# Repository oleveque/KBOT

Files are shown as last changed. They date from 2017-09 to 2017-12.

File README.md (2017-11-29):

# KBOT

Un KBOT est un petit "robot sandwich" doté de deux roues motrices (moteurs+codeurs), d'une Arduino Méga 2560, d'un écran LCD 16x2, d'une batterie 3S… C'est une fabrication maison que réalise les premières années du club de robotique de l'ENS Paris-Saclay pour acquérir les bases de la robotique & se familiariser avec la programmation à travers l'IDE Arduino.
Pour plus d'information consultez notre site [[Kro]bot](https://wiki.crans.org/ClubKrobot).

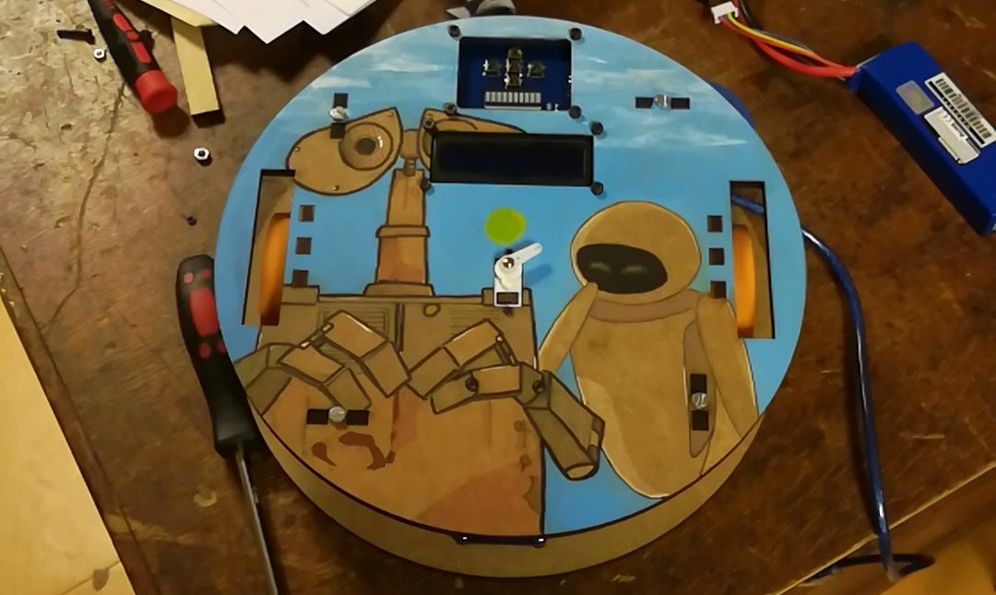
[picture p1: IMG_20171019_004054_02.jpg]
KBOT_V2


## Informations générales :
* *Mode de déplacement du robot :* entraînement différenciel
* *Moyens de communication :* USB, Bluetooth
* *Version actuelle :* 2.0 (Révisé par Y. Labbe & O. Lévêque - Sept. 2017)

## Ports I/O :
* 1 module Bluetooth (HC-06) ;
* 1 port SHARP (GP2D12) ;
* 1 port Servo (SG90) ;
* 1 port pour controler le niveau de charge de la batterie ;
* 1 Buzzer ;
* 1 port extension pour 5 Boutons ;
* 1 port extension pour 10 Leds.

## Amélioration pour la version 2.1 :
* CAO -> simplifier les entretoises des roues + ajuster l'empreinte de l'écran LCD + ajouter un système de fixations pour les cales avant/arrière
* PCB -> corriger l'agencement buzzer/bluetooth + corriger les couleurs des fils des encoders + changer le sens de la nappe PowerDistributor-PropulsionShield + changer le sens de connecteur batterie + amener la led 13 sur le UI
* Arduino -> Ajouter 1 exemple d'Asserv

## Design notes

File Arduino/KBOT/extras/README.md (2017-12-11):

# KBOT + BRAINZY

Vous pouvez utiliser la bibliothèque BRAINZY pour programmer votre KBOT : http://github.com/oleveque/BRAINZY
Une documentation complète de cette bibliothèque est disponible : http://docs.mr-robotics.com

## Installation

Une fois la bibiliothèque BRAINZY installée sur votre ordinateur, il ne reste plus qu'à remplacer les fichiers
`BRAINZY > src > utility > configRobot.h` et `BRAINZY > src > utility > config_v3.0.h` par les deux fichiers fournis dans `KBOT > extras`.
N'oubliez pas de faire correspondre les fichiers changés avec ceux appelés par le fichier `BRAINZY > src > BRAINZY.h`.

Enjoy & have a lot of fun...
Made with love by [Kro]bot team.

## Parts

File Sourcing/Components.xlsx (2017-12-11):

 | Batch ($) | Qty (Batch) | Unit ($) | Unit (€) | Qty | TOT 1 KBot (€) | Mots clés (Recherche ebay/Aliexpress)
Composants mécaniques & éléctrique
Moteur (http://www.robotshop.com/eu/fr/moteur-12v-150rpm-a-engrenage-301-avec-encodeur.html) |  |  |  | 21.86 | 2 | 43.72
Hex mount (http://www.robotshop.com/eu/fr/moyeu-hex-6mm-1l.html) |  |  |  | 4.31 | 2 | 8.62
Roue 2-7/8" (http://www.robotshop.com/eu/fr/rb-ban-94-roue-orange.html) |  |  |  | 3.2 | 2 | 6.4
Arduino Mega 2560 (https://fr.aliexpress.com/item/Free-Shipping-MEGA2560-R3-MEGA2560-REV3-ATMEGA2560-16AU-Board-USB-Cable-compatible-We-are-the-manufacturer/32513419382.html) |  |  | 9.57 | 8.12 | 1 | 8.12 | Arduino Mega 2560
Pont (dual) L298N (https://www.aliexpress.com/item/Free-Shipping-10pcs-lot-L298N-Dual-Bridge-DC-stepper-Controller-Control-Motor-Driver-module-Board/32581277003.html) | 14.85 | 10 | 1.49 | 1.26 | 1 | 1.26 | L298N
Chargeur (http://www.ebay.com/itm/iMaxRC-iMax-B3-Pro-Compact-2S-3S-Lipo-Balance-Battery-Charger-For-RC-Helicopter-/172802158295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) |  |  |  | 4 | 1 | 4 | Lipo 3S charger
Batterie 3S-2200 mAh (https://hobbyking.com/fr_fr/turnigy-2200mah-3s-25c-lipo-pack.html) |  |  |  | 9.36 | 1 | 9.36
1602 LCD + I2C (https://www.aliexpress.com/item/1602-16x2-HD44780-Character-LCD-w-IIC-I2C-Serial-Interface-Adapter-Module/32709905064.html) |  |  |  | 1.46 | 1 | 1.46 | 1602 lcd + i2c
Bluetooth (https://www.aliexpress.com/item/4pin-hc-06-Bluetooth-transmission-module-including-base-plate-belt-enable-and-output-radio-serial/32265012433.html) |  |  |  | 1.46 | 1 | 2.4 | HC-06
Servomoteur 9G SG90 (https://fr.aliexpress.com/item/Free-Shipping-10pcs-lot-Special-promotions-SG90-9g-Mini-Micro-Servo-for-RC-for-RC-250/32320058558.html) |  |  | 1.22 | 1.04 | 1 | 1.04 | SG90 9G
Sharp 10-80cm (https://fr.aliexpress.com/item/IR-Sensor-GP2Y0A21YK0F-Measuring-Detecting-Distance-Sensor-10-to-80cm-with-Cable-for-Arduino/32462134213.html) |  |  |  | 3.1 | 1 | 3.1 | Sharp sensor 10-80cm
Sous-total |  |  |  |  |  | 89.48
Connectique
Nappe JST 2.54mm f-f 4pin 20cm Power <-> Shield (https://www.aliexpress.com/item/100-SETS-JST-XH-2-54mm-2-3-4-5-6-7-8-9-10-Pin/32794829177.html) | 20.89 | 100 | 0.21 | 0.18 | 1 | 0.18 | Jst wire double end
JST 2.54mm 4 pin connecteur m (https://fr.aliexpress.com/item/150Pcs-2-54Mm-Pitch-Male-4-Pins-Rc-Lipo-Battery-Balance-Connector-Jst-Xh-Header/32768115241.html) | 2.91 | 150 | 0.02 | 0.02 | 2 | 0.03
Nappe JST2.0 mm f-f 3pin 20cm Sharp <-> Shield (https://www.aliexpress.com/item/100-SETS-JST-PH-2-0mm-2-3-4-5-6-7-8-9-10-Pin/32797675782.html) | 19.94 | 100 | 0.2 | 0.17 | 1 | 0.17 | Jst wire double end
JST 2.0mm 3 pin connecteur m (http://www.ebay.com/itm/JST-PH-2-0mm-3-Pin-Male-and-Female-Housing-Connector-with-Crimps-x-50-Sets-/122329707743) | 6.17 | 50 | 0.12 | 0.1 | 1 | 0.1
Nappe Dupont f-f 4pin 20cm I2C-Screen <-> Shield (https://www.aliexpress.com/item/NEW-10pcs-lot-Keyestudio-4-PIN-20CM-jumper-wire-dupont-cable-for-arduino-breadboard-free-shipping/32706947085.html) | 2.66 | 10 | 0.27 | 0.23 | 1 | 0.23 | Dupont 4 pin wire
Fil dupont vert f-f 20cm Moteur G <-> Shield (https://www.aliexpress.com/item/Free-shipping-100pcs-New-1p-to-1p-20cm-Green-female-to-female-jumper-wire-Dupont-cable/1790303724.html) | 5 | 100 | 0.05 | 0.04 | 2 | 0.08 | female to female dupont green wire
Fil dupont bleu f-f 20cm Moteur D <-> Shield (https://www.aliexpress.com/item/Free-shipping-100pcs-New-1p-to-1p-20cm-Red-female-to-female-jumper-wire-Dupont-cable/1790340551.html) | 5 | 100 | 0.05 | 0.04 | 2 | 0.08
Dupont 2 pin housing f (https://fr.aliexpress.com/item/200Pcs-2P-Dupont-Jumper-Wire-Cable-Housing-Plug-Female-Pin-Terminal-Dupont-Shell-Kit-Connector-2/32630018317.html) | 1.75 | 200 | 0.01 | 0.01 | 2 | 0.01 | female to female dupont blue wire
Nappe Nu-JST 2.54mm 4pin 15cm Codeur <-> Shield + Connecteur (https://www.aliexpress.com/item/Promotion-10Pcs-3S-JST-XH-Connector-Adapter-plug-4-Pin-Servo-Extension-Cord-15CM/32622982969.html) | 1.08 | 100 | 0.01 | 0.01 | 2 | 0.02 | JST-XH 4 pin wire
Nappe Nu-JST 2.54mm 2pin 20cm Driver <-> Shield + Connecteur (http://www.ebay.com/itm/20-Set-Jst-Xh-2-5-2-Pin-Connector-Plug-Male-With-200mm-Wire-Female-Connect-/331834666362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) | 3.59 | 20 | 0.18 | 0.15 | 1 | 0.15 | JST 2.54mm 2 pin wire
Nappe 2x5 pin 15cm UI <-> Shield (https://cart.payments.ebay.com/sc/view) | 3.59 | 5 | 0.72 | 0.61 | 2 | 1.22 | 2x5 ribbon cable 10cm
2x5 Connecteur DIP m (http://www.ebay.com/itm/131881379942) | 2.39 | 20 | 0.12 | 0.1 | 4 | 0.41
Prise Jack Femelle CMS (https://fr.aliexpress.com/item/10PCS-LOT-SMD-DC-005-DC-Power-Jack-Socket-Connector-DC005-5-5-2-1mm-2/32730853300.html) | 1.65 | 10 | 0.17 | 0.14 | 1 | 0.14
Connecteur JST 2.54mm 4pin coudé (https://fr.aliexpress.com/item/100pcs-Hot-2-54mm-XH2-54-4P-Right-Angle-Socket-Connector-Bent-Pin-Header/32612476896.html) | 3.31 | 100 | 0.03 | 0.03 | 1 | 0.03 | Right-angle jst 2.54mm
Bornier 5mm 2pin (https://fr.aliexpress.com/item/100-pcs-2-Pin-Screw-blue-PCB-Terminal-Block-Connector-5mm-Pitch-Green/32627128431.html) | 7.8 | 50 | 0.16 | 0.13 | 1 | 0.13 | Terminal 5mm 2pin
Fil Jack-XT60 batterie (https://fr.aliexpress.com/item/T-XT60-Male-Plug-to-5-5mm-DC-Plug-Jack-Cable-Adapter-DC5521-Connect-Lipo-Battery/32828289009.html) |  |  | 1.42 | 1.2 | 1 | 1.2 | Jack to XT60
Sous-total |  |  |  |  |  | 4.19
Composants PCB
Boutton poussoir 6*6*5mm DIP (https://fr.aliexpress.com/item/1000-Pcs-Tactile-Switch-Tact-6x6x5-Mm-4-pin-Inline-Dip-micro-s-Top-Copper-Power/32696220912.html) | 10.13 | 1000 | 0.01 | 0.01 | 7 | 0.06 | 6*6*5mm tactile switch 1000pcs
Bar Graph 10 segment Rouge (https://fr.aliexpress.com/item/10PCS-10-Segment-Digital-Red-LED-Bar-Graph-Display-Ultra-Bright/32581756668.html) | 1.78 | 10 | 0.18 | 0.15 | 1 | 0.15 | bar graph 10 segment red
Buzzer (https://fr.aliexpress.com/item/Free-Shipping-100pcs-Universal-passive-buzzer-electromagnetic-impedance-16-ohms-AC-2KHz-3V-5V-12V-Universal/32763380359.html) | 6.24 | 100 | 0.06 | 0.05 | 1 | 0.05 | Buzzer
Led CMS 1206 bleue (https://fr.aliexpress.com/item/100-PCS-1206-Bleu-Led-Super-Lumineux-SMD-LED-diodes-3-2-1-6-0-8/32676224740.html) | 0.67 | 100 | 0.01 | 0.01 | 2 | 0.01 | LED SMD 1206 blue
Led CMS 1206 rouge (https://fr.aliexpress.com/item/100PCS-LOT-1206-Red-SMD-LED-Diode-Light-3216-Diodes-SMD-Super-Bright-1206-led-3/32623813733.html) | 0.99 | 100 | 0.01 | 0.01 | 1 | 0.01 | LED SMD 1206 red
Led 5mm bicolor vert-rouge (https://fr.aliexpress.com/item/100pcs-LED-5mm-Round-Diffused-Red-Green-two-Color-Common-Cathode-LED-Diode-Light-Emitting-Diode/32278849344.html) | 4.68 | 100 | 0.05 | 0.04 | 1 | 0.04
Resistance 1206 470k (https://fr.aliexpress.com/item/1206-SMD-Resistor-5-330K-ohm-5000pcs-lot/32308252576.html) | 1.58 | 500 | 0 | 0 | 2 | 0.01
Resistance 1206 240k (https://fr.aliexpress.com/item/1206-SMD-Resistor-5-200K-ohm-5000pcs-lot/32307106612.html) | 1.58 | 500 | 0 | 0 | 2 | 0.01
Resistance 1206 1k (https://fr.aliexpress.com/item/1206-SMD-Resistor-5-1K-ohm-5000pcs-lot/32307138058.html) | 1.58 | 500 | 0 | 0 | 7 | 0.02
Resistance 1206 2k (https://fr.aliexpress.com/item/1206-SMD-Resistor-5-1-6K-ohm-5000pcs-lot/32307090605.html) | 1.58 | 500 | 0 | 0 | 1 | 0
Resistance 1206 470 (https://fr.aliexpress.com/item/1206-SMD-Resistor-5-390-ohm-5000pcs-lot/32307090602.html) | 1.58 | 500 | 0 | 0 | 13 | 0.03 | Bicolor led green red
Condensateur 1206 10µ (https://fr.aliexpress.com/item/100PCS-LOT-10uf-Error-10-50V-106-10UF-1206-SMD-Thick-Film-Chip-Multilayer-Ceramic-Capacitor/32818359105.html) | 1.6 | 100 | 0.02 | 0.01 | 1 | 0.01
Sous-total |  |  |  |  |  | 0.4
PCBs
PCB - Shield (http://www.electrodragon.com/product/pcb-service/) |  |  |  |  | 1 | 4.5
PCB - Power Distributor (http://www.electrodragon.com/product/pcb-service/) |  |  |  |  | 1
PCB - User Interface (http://www.electrodragon.com/product/pcb-service/) |  |  |  |  | 1
Sous-total |  |  |  |  |  | 4.5
Bois & Visserie |  |  |  |  |  |  | Bricovis
Bois - Découpe Laser (https://www.sculpteo.com/fr/) |  |  |  |  |  | 23.5
Ecrou M3 |  |  |  | 0.01 | 28 | 0.28 | ECRHU03BR
Ecrou M4 |  |  |  | 0.01 | 8 | 0.08 | ECRHU04BR
Vis entretoise |  |  |  | 0.06 | 8 | 0.48 | TRL04/020ZN
Vis moteurs |  |  |  | 0.02 | 6 | 0.12 | TCL03/010ZN
Vis cartes arduino |  |  |  | 0.07 | 20 | 1.4 | TCHC03/016A8NOEF
petites vis servo |  |  |  |  |  |  | A trouver
Vis longue arduino |  |  |  | 0.2 | 1 | 0.2 | TCHC03/035A8NOPF
Patins teflon
Sous-total |  |  |  |  |  | 26.06
TOTAL |  |  |  |  |  | 124.64
Alternatives
Hex mount (http://www.banebots.com/mm5/merchant.mvc?Screen=PROD&Store_Code=banebots&Product_Code=T40H-SM61) |  |  |  | 4.4 | 2 | 8.8
Roue 2-7/8" (http://www.banebots.com/product/T40P-295BA-HS4.html) |  |  |  | 3.3 | 2 | 6.6
Prise Jack Male (https://fr.aliexpress.com/item/2016-Hot-Sales-5-Pcs-Black-2-1mm-x-5-5mm-DC-Power-Male-Plug-Jack/32655336652.html) | 0.95 | 5 | 0.19 | 0.16 | 1 | 0.16
Prise XT-60 Batterie (https://fr.aliexpress.com/item/10pair-lot-XT60-bullet-Connectors-plugs-Male-Female-RC-lipo-free-shipping/388573167.html) | 1.87 | 10 | 0.19 | 0.16 | 1 | 0.16

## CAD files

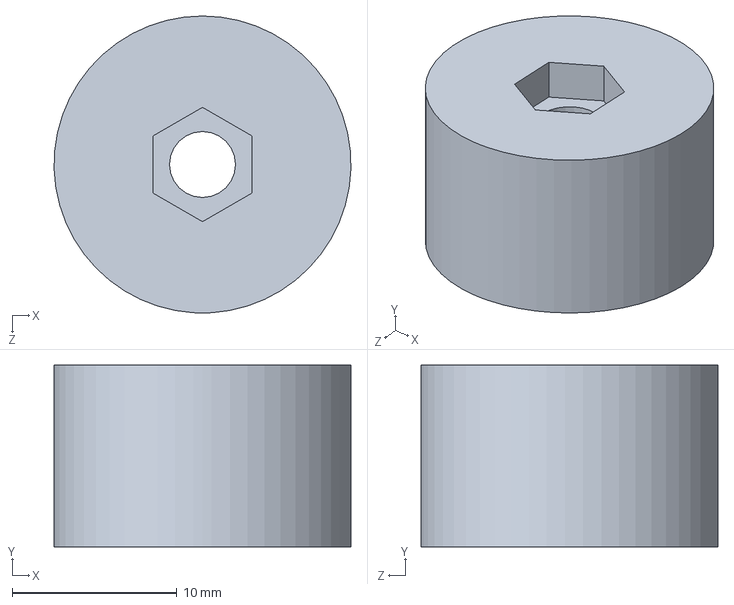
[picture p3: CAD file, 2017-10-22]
CAO/3D printing parts/skate-support.SLDPRT
18.0 x 11.0 x 18.0 mm

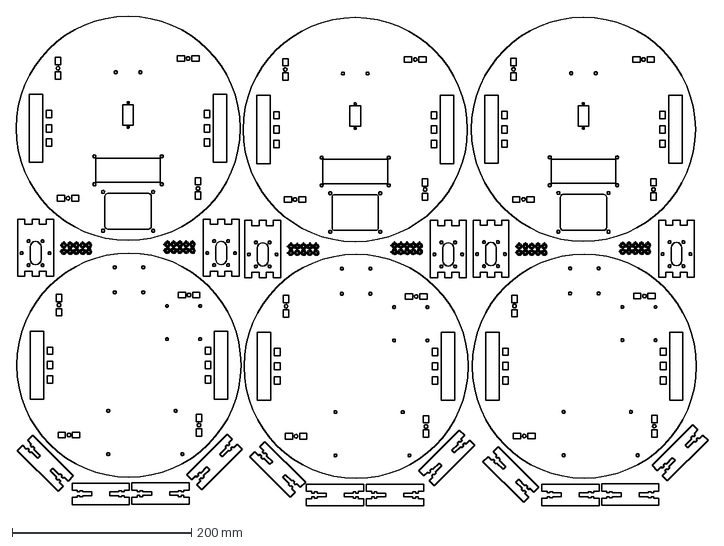
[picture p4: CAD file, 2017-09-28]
CAO/Laser-cut Parts/3-kbots.DXF
771.8 x 545.9 mm

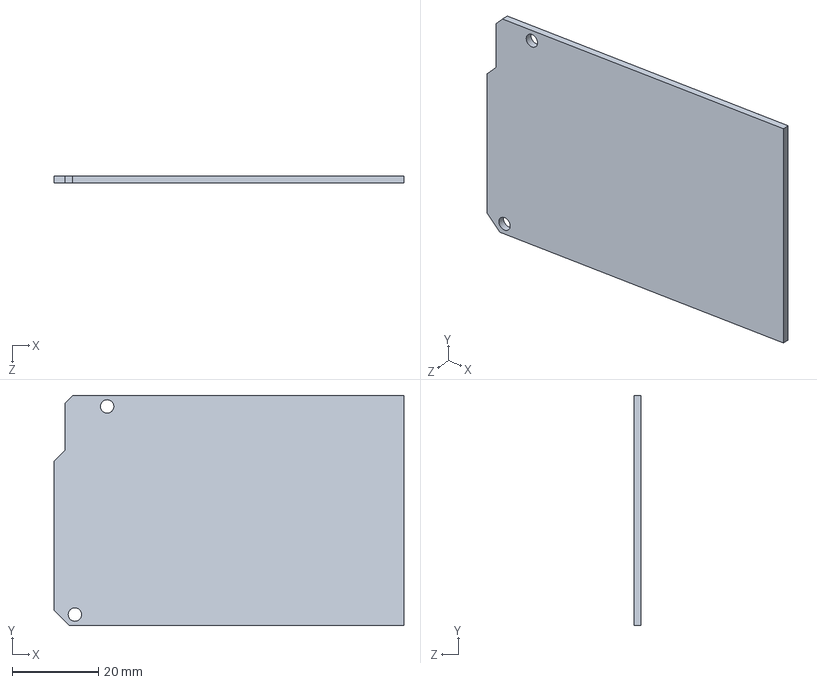
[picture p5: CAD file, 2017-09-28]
CAO/Other parts/Electronics/propulsion-shield.SLDPRT
81.3 x 53.4 x 1.65 mm

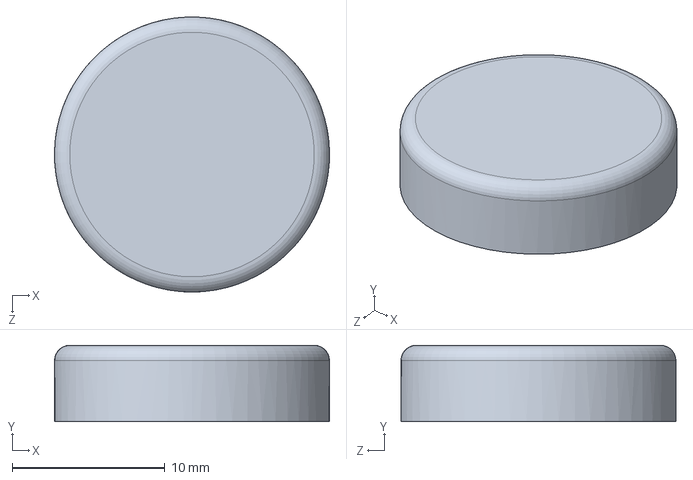
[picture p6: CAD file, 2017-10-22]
CAO/Other parts/skate.SLDPRT
18.0 x 5.00 x 18.0 mm

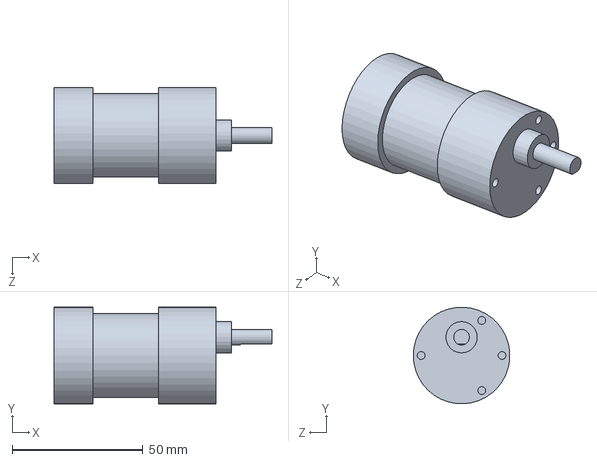
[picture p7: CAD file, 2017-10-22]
CAO/Other parts/Wheel/motor.SLDPRT
83.5 x 37.0 x 36.9 mm

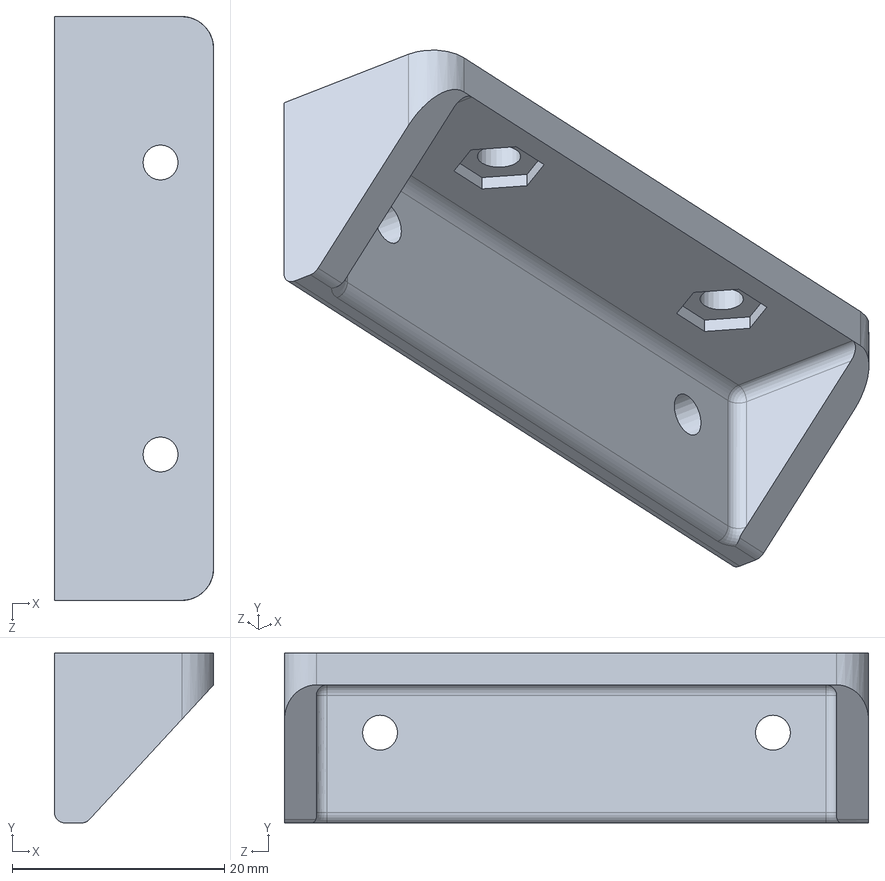
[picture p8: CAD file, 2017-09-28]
CAO/3D printing parts/sharp-support.SLDPRT
15.0 x 16.0 x 55.0 mm

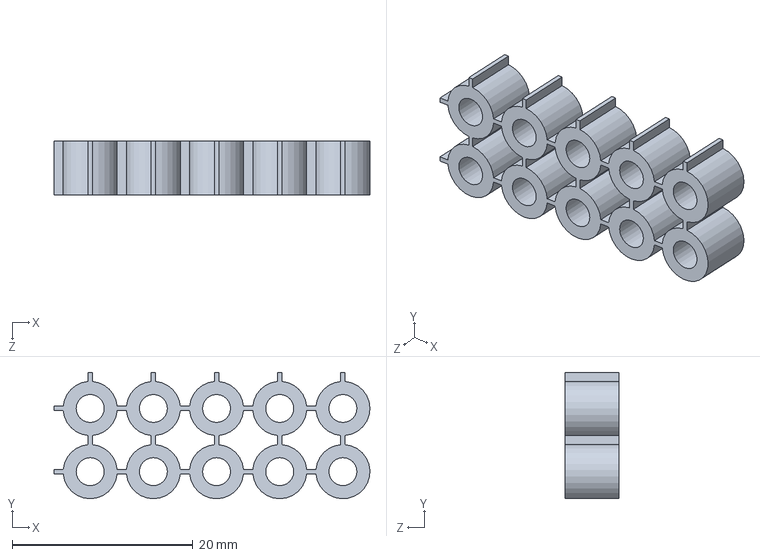
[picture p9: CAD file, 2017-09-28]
CAO/Laser-cut Parts/matrix-brace.SLDPRT
35.0 x 14.0 x 6.00 mm

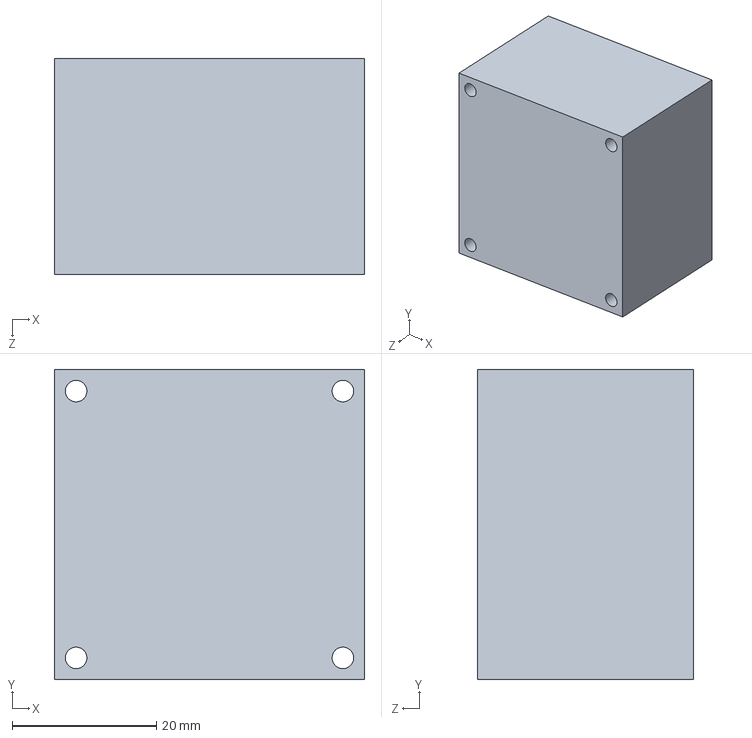
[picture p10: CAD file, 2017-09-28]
CAO/Other parts/Electronics/bridge.SLDPRT
43.0 x 43.0 x 30.0 mm

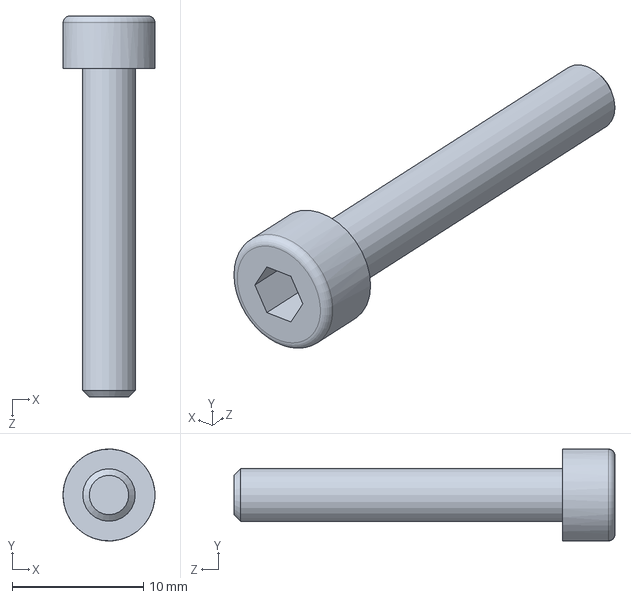
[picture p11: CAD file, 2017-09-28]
CAO/Other parts/m4.SLDPRT
7.00 x 7.00 x 29.0 mm

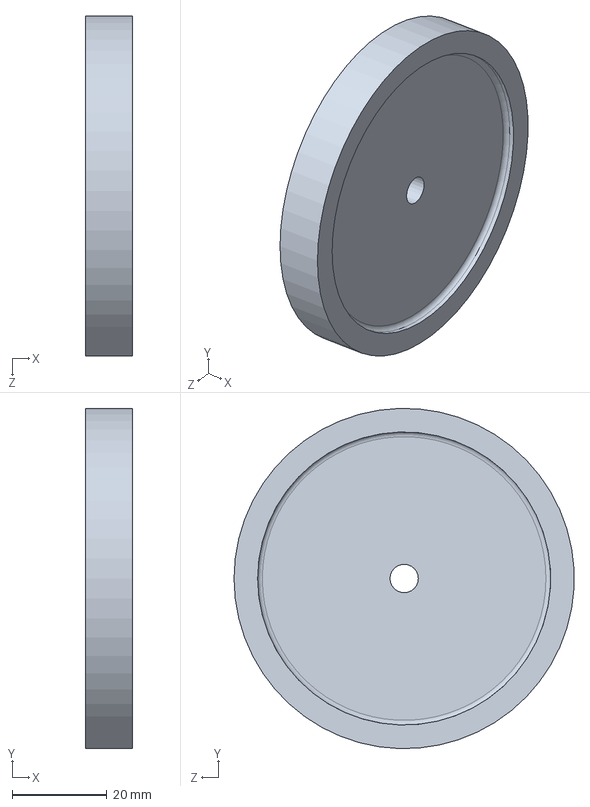
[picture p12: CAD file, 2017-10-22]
CAO/Other parts/Wheel/wheel.SLDPRT
10.0 x 72.0 x 71.9 mm

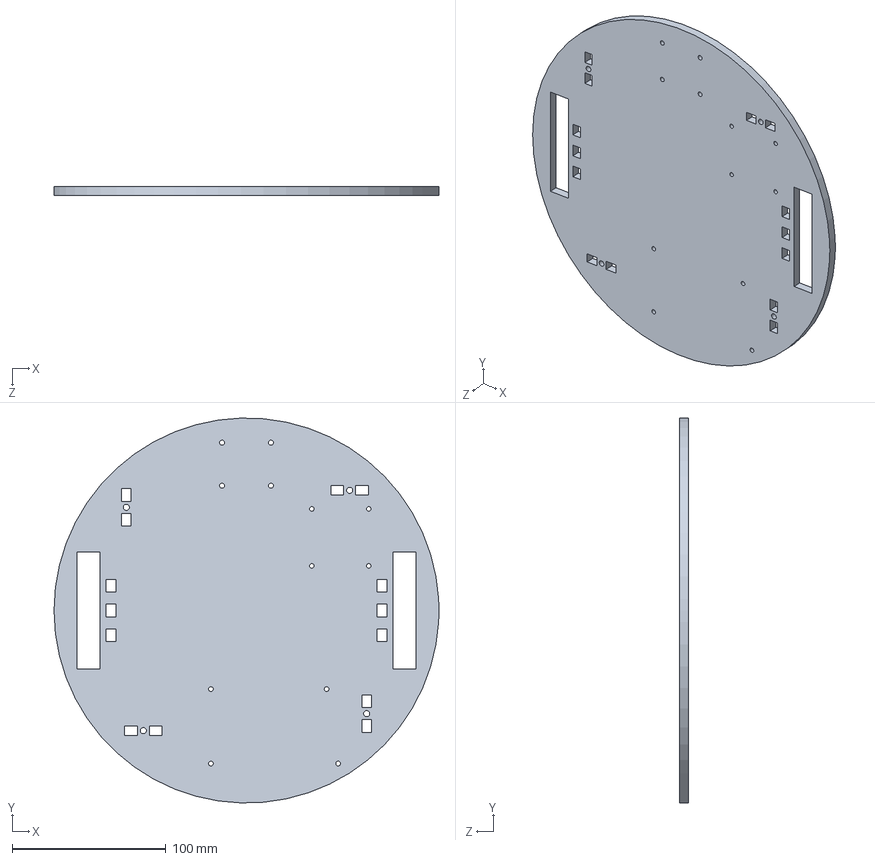
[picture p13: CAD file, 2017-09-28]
CAO/Laser-cut Parts/socle1.SLDPRT
250.0 x 249.9 x 6.00 mm

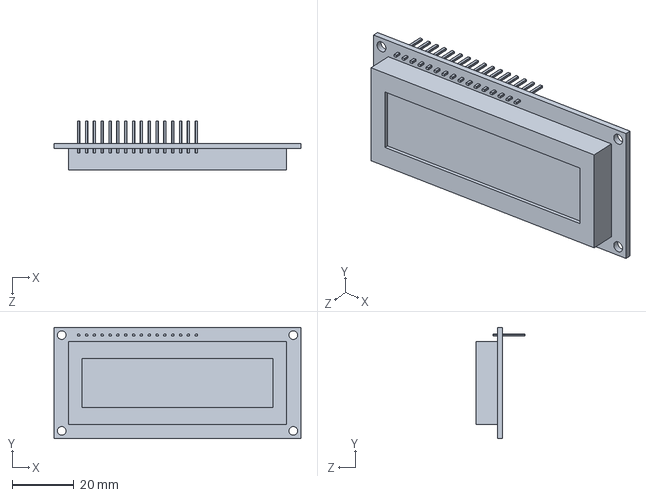
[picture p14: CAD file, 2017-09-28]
CAO/Other parts/Electronics/screen.SLDPRT
80.0 x 36.0 x 16.0 mm

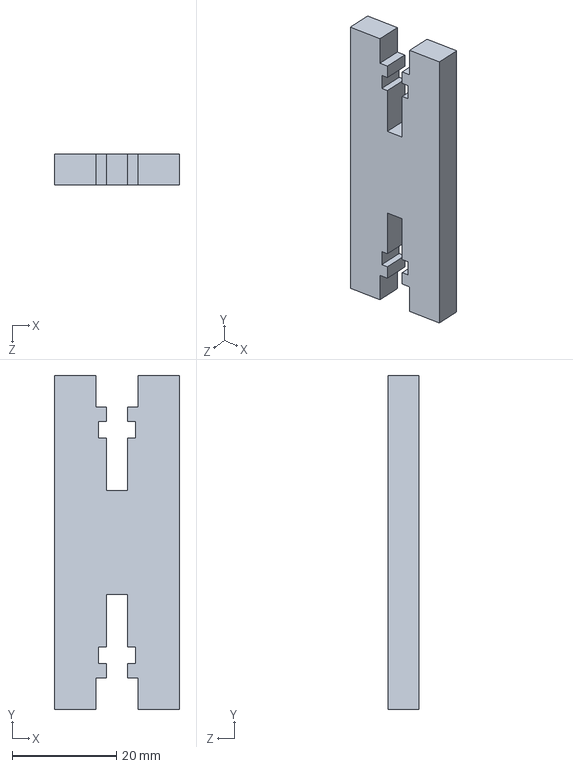
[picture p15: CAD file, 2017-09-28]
CAO/Laser-cut Parts/brace.SLDPRT
24.0 x 64.0 x 6.00 mm

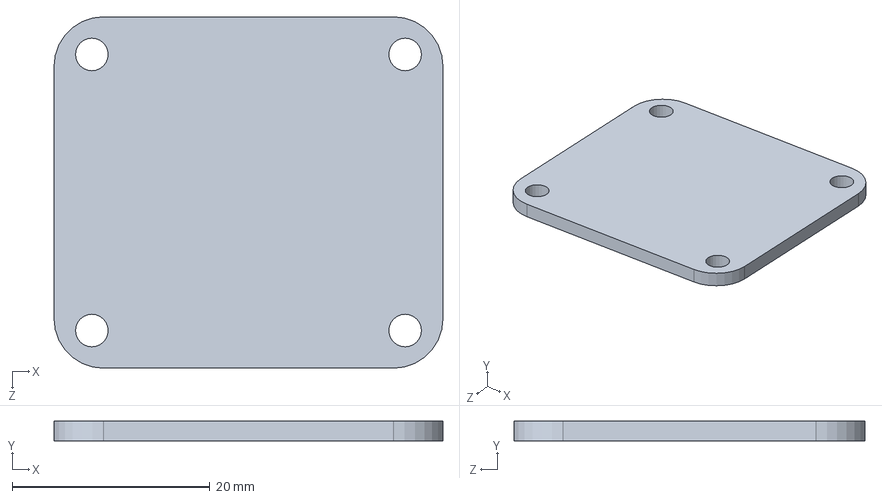
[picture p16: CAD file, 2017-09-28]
CAO/Other parts/Electronics/power-shield.SLDPRT
39.4 x 2.00 x 35.6 mm

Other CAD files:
CAO/Laser-cut Parts/1-kbot.DXF
CAO/Other parts/Electronics/battery.SLDPRT
CAO/Laser-cut Parts/brace-motor.SLDPRT
CAO/Other parts/Electronics/arduino.SLDPRT
CAO/3D printing parts/sharp-support.STL
CAO/3D printing parts/skate-support.STL
CAO/Laser-cut Parts/1-kbot.SLDDRW
CAO/Laser-cut Parts/3-kbots.SLDDRW
CAO/Laser-cut Parts/socle2.SLDPRT
CAO/Other parts/Electronics/user-interface.SLDPRT

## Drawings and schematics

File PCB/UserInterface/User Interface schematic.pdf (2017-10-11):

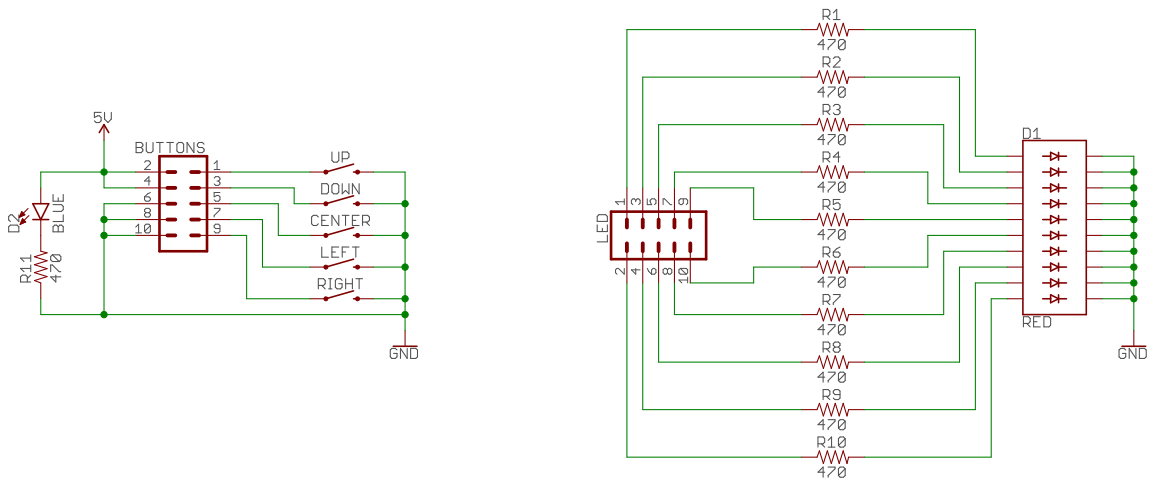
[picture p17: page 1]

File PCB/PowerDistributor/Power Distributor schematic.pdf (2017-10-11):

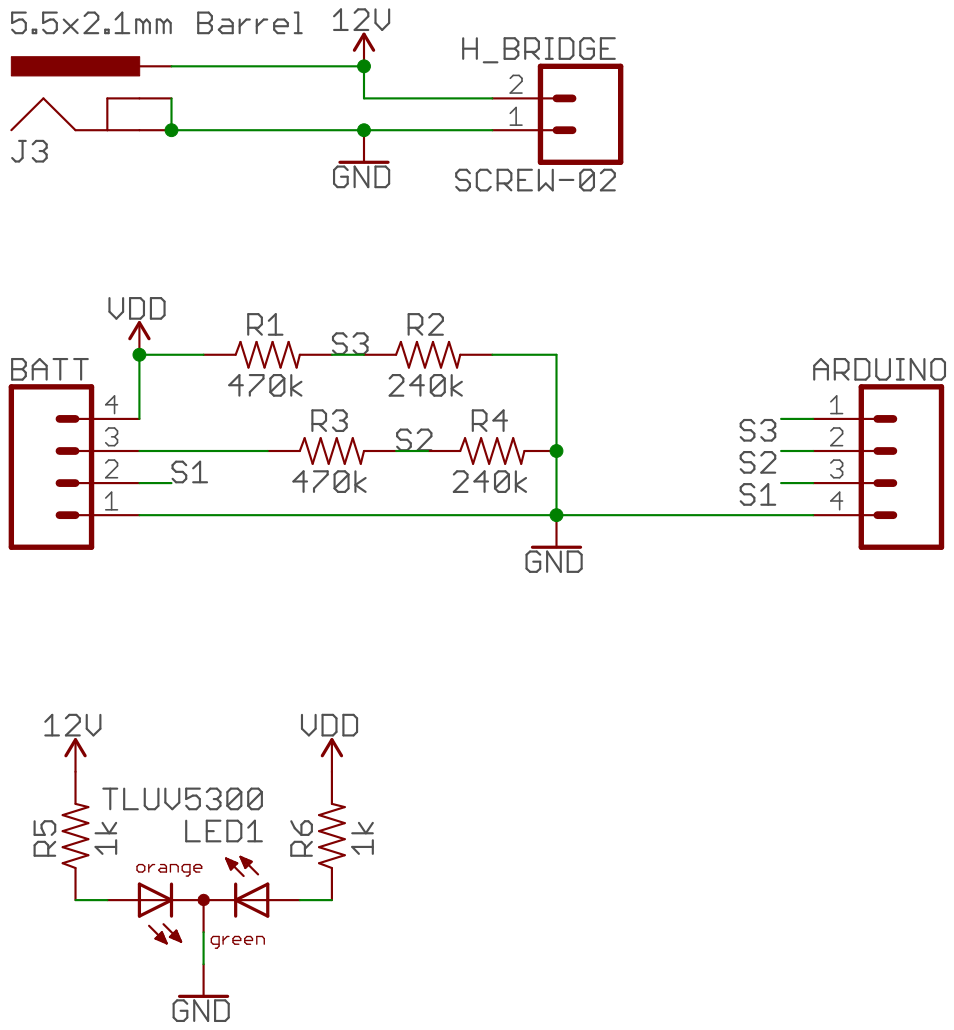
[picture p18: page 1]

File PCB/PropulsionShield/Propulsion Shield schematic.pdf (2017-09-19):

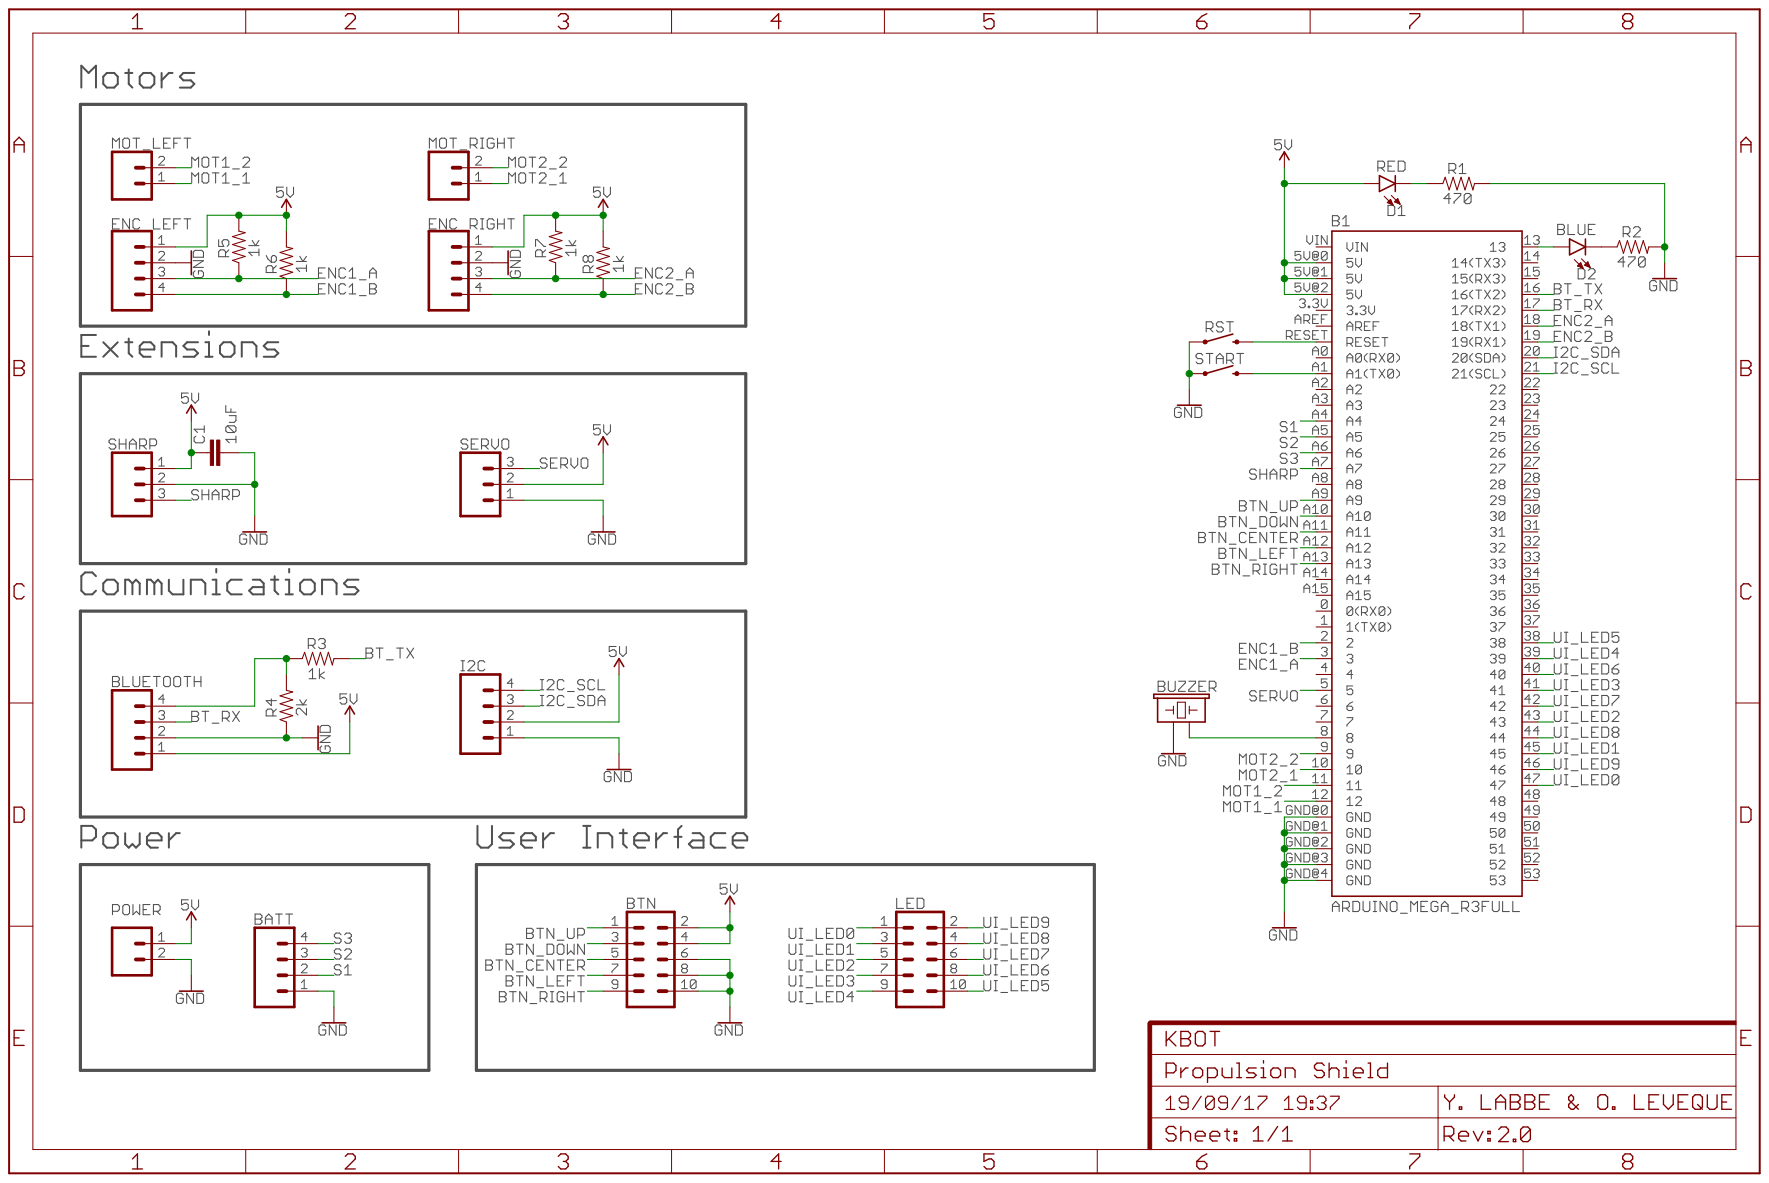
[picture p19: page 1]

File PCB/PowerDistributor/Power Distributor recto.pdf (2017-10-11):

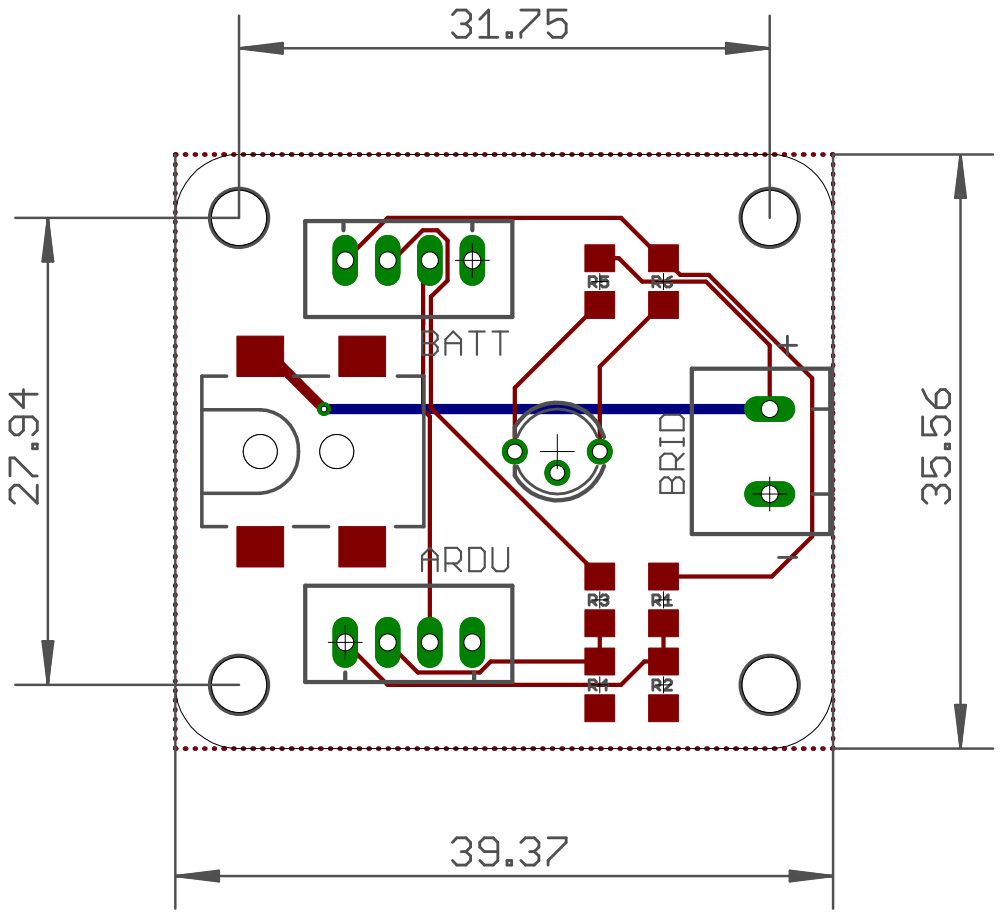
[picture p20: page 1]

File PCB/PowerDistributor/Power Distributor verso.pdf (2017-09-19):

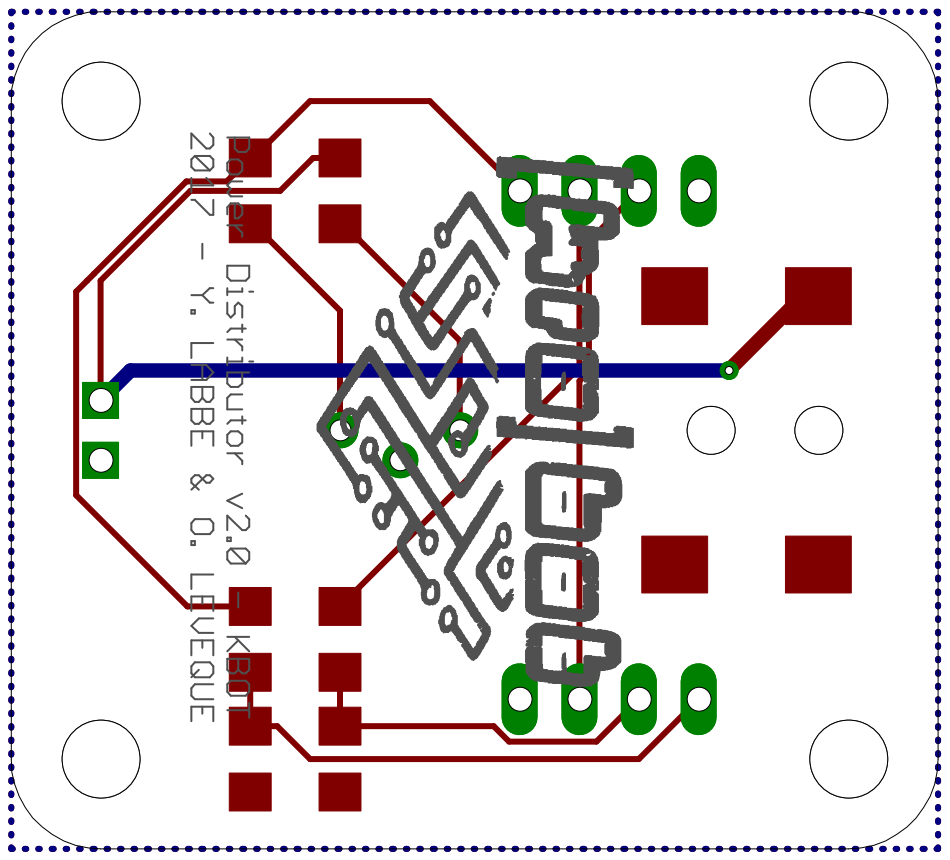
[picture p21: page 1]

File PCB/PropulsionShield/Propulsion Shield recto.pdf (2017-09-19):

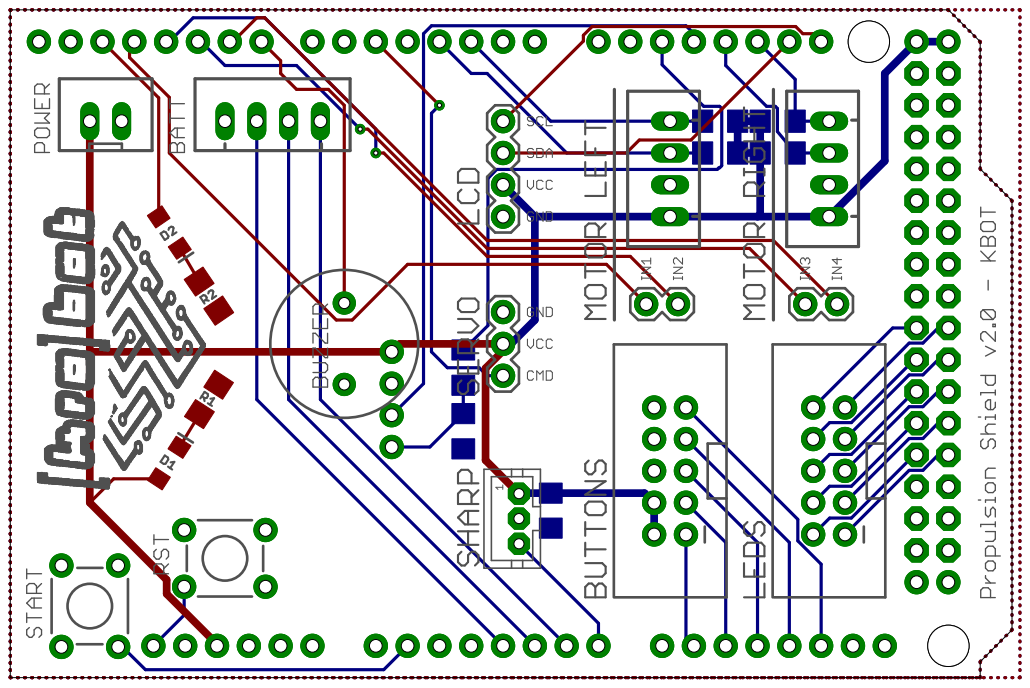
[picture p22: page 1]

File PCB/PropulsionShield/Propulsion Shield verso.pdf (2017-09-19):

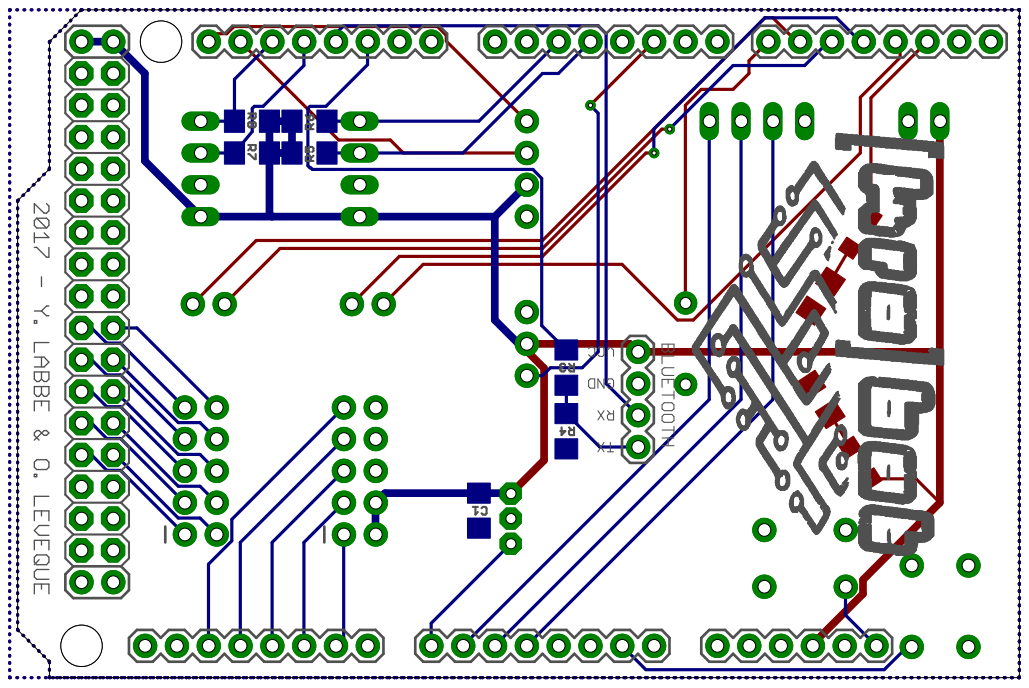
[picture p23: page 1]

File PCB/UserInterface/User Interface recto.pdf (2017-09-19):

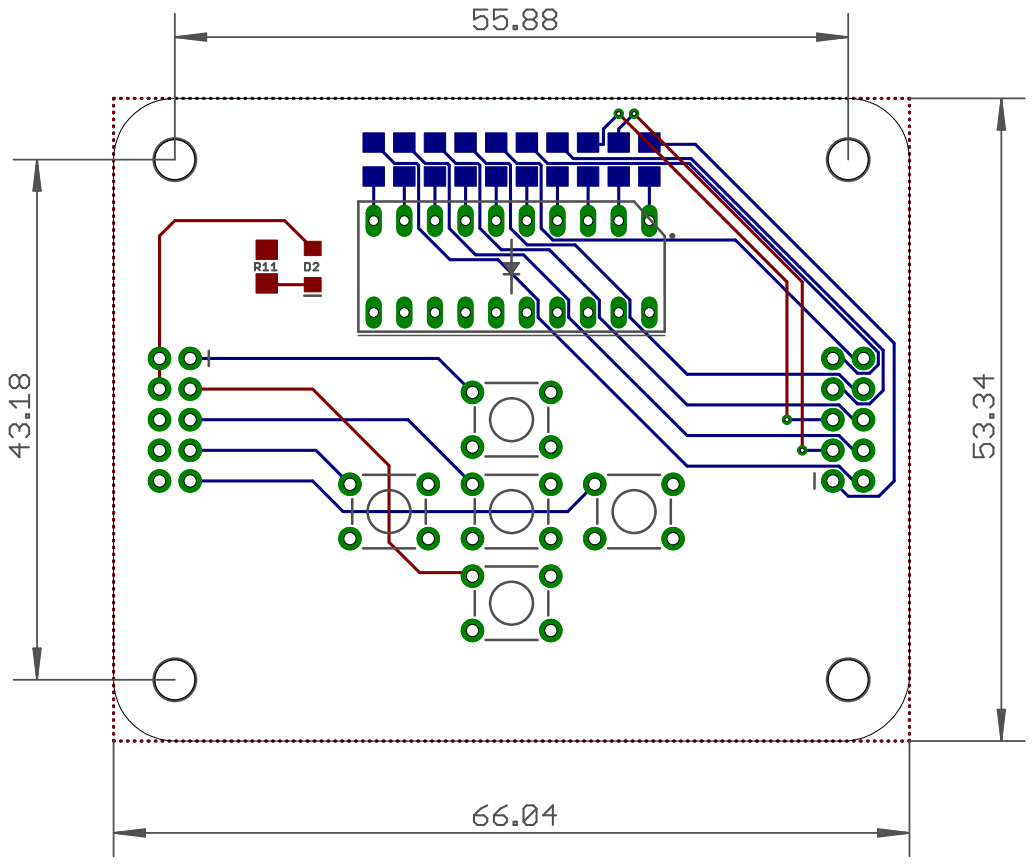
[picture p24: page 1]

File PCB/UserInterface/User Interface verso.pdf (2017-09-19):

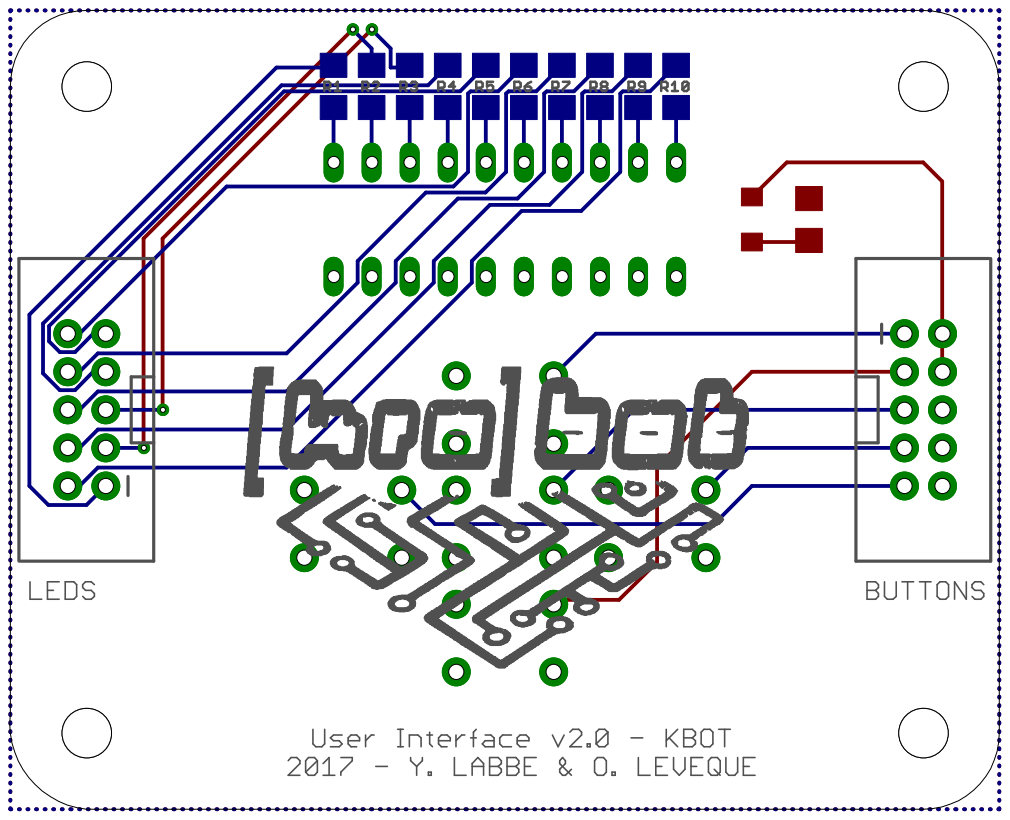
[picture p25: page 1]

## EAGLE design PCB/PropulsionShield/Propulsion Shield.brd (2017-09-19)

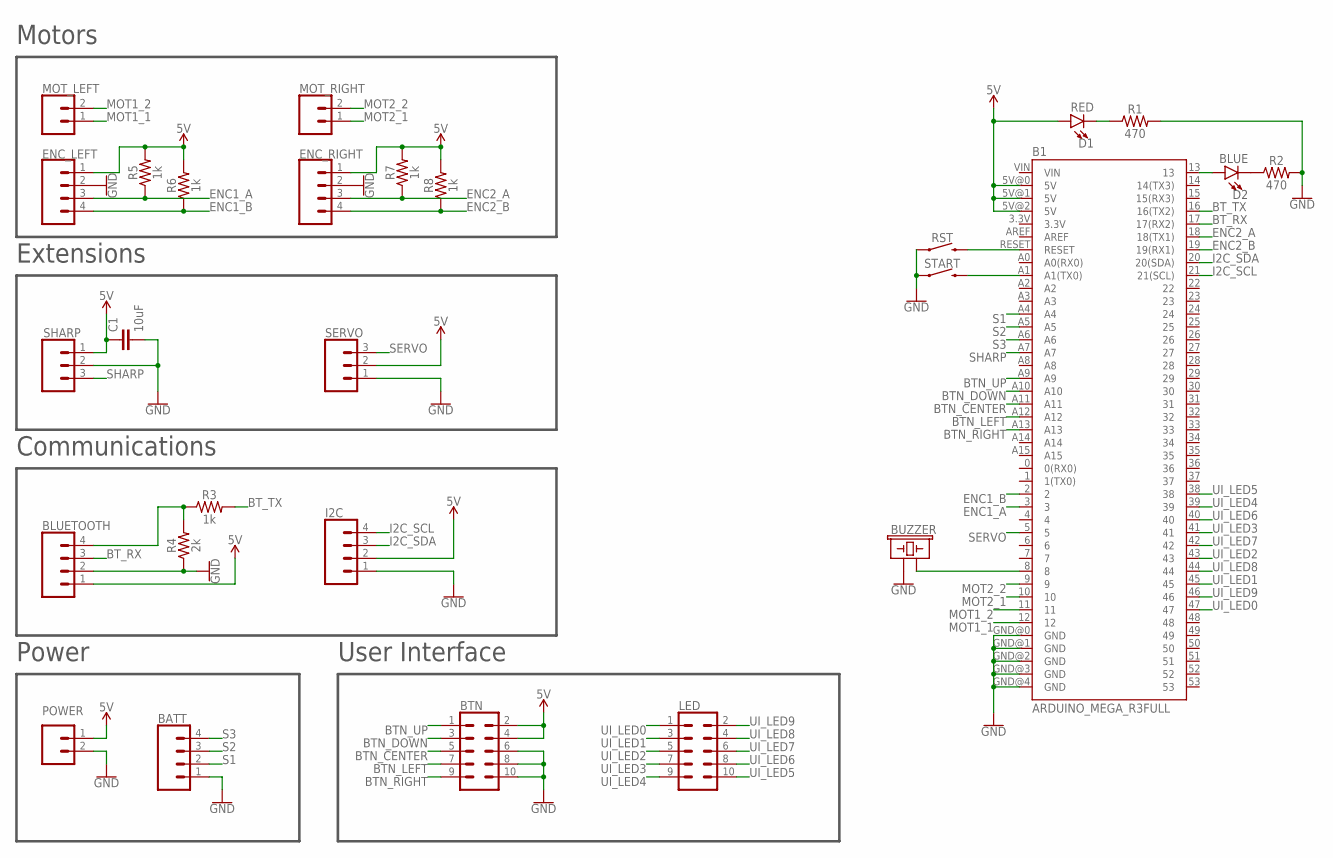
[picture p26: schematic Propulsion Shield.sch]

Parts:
B1: ARDUINO_MEGA_R3FULL; ARDUINO_MEGA
BATT: JST-XH-04-PIN-LONG-PAD; JST-XH-04-PACKAGE-LONG-PAD
BLUETOOTH: CONN_04; 1X04
BTN: CONN_05X2SHD; 2X5-SHROUDED
BUZZER: BUZZER-PTH; BUZZER-12MM
C1: 10uF; 1206
D1: RED; LED-1206
D2: BLUE; LED-1206
ENC_LEFT: JST-XH-04-PIN-LONG-PAD; JST-XH-04-PACKAGE-LONG-PAD
ENC_RIGHT: JST-XH-04-PIN-LONG-PAD; JST-XH-04-PACKAGE-LONG-PAD
I2C: CONN_04; 1X04
LED: CONN_05X2SHD; 2X5-SHROUDED
MOT_LEFT: CONN_02; 1X02
MOT_RIGHT: CONN_02; 1X02
POWER: JST-XH-02-PIN-LONG-PAD; JST-XH-02-PACKAGE-LONG-PAD
R1, R2: 470; 1206
R3, R5, R6, R7, R8: 1k; 1206
R4: 2k; 1206
RST: MOMENTARY-SWITCH-SPST-PTH-6.0MM; TACTILE_SWITCH_PTH_6.0MM
SERVO: CONN_03; 1X03
SHARP: JST-PH3
START: MOMENTARY-SWITCH-SPST-PTH-6.0MM; TACTILE_SWITCH_PTH_6.0MM

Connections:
5V: B1.5V@0 (5V), B1.5V@1 (5V), B1.5V@2 (5V), BLUETOOTH.1, BTN.2, BTN.4, C1.1, D1.A, ENC_LEFT.1, ENC_RIGHT.1, I2C.2, POWER.1, R5.2, R6.2, R7.2, R8.2, SERVO.2, SHARP.1
BTN_CENTER: B1.A11, BTN.5
BTN_DOWN: B1.A10, BTN.3
BTN_LEFT: B1.A12, BTN.7
BTN_RIGHT: B1.A13, BTN.9
BTN_UP: B1.A9, BTN.1
BT_RX: B1.17 (17(RX2)), BLUETOOTH.3
BT_TX: B1.16 (16(TX2)), R3.2
BUZZER: B1.8, BUZZER.- (2)
ENC1_A: B1.3, ENC_LEFT.3, R5.1
ENC1_B: B1.2, ENC_LEFT.4, R6.1
ENC2_A: B1.18 (18(TX1)), ENC_RIGHT.3, R7.1
ENC2_B: B1.19 (19(RX1)), ENC_RIGHT.4, R8.1
GND: B1.GND@0 (GND), B1.GND@1 (GND), B1.GND@2 (GND), B1.GND@3 (GND), B1.GND@4 (GND), BATT.1, BLUETOOTH.2, BTN.6, BTN.8, BTN.10, BUZZER.+ (1), C1.2, ENC_LEFT.2, ENC_RIGHT.2, I2C.1, POWER.2, R1.2, R2.2, R4.1, RST.1, SERVO.1, SHARP.2, START.1
I2C_SCL: B1.21 (21(SCL)), I2C.4
I2C_SDA: B1.20 (20(SDA)), I2C.3
MOT1_1: B1.12, MOT_LEFT.1
MOT1_2: B1.11, MOT_LEFT.2
MOT2_1: B1.10, MOT_RIGHT.1
MOT2_2: B1.9, MOT_RIGHT.2
unnamed: B1.RESET, RST.3 (2)
unnamed: D1.C, R1.1
unnamed: B1.13, D2.A
unnamed: D2.C, R2.1
unnamed: BLUETOOTH.4, R3.1, R4.2
unnamed: B1.A1 (A1(TX0)), START.3 (2)
S1: B1.A4, BATT.2
S2: B1.A5, BATT.3
S3: B1.A6, BATT.4
SERVO: B1.5, SERVO.3
SHARP: B1.A7, SHARP.3
UI_LED0: B1.47, LED.1
UI_LED1: B1.45, LED.3
UI_LED2: B1.43, LED.5
UI_LED3: B1.41, LED.7
UI_LED4: B1.39, LED.9
UI_LED5: B1.38, LED.10
UI_LED6: B1.40, LED.8
UI_LED7: B1.42, LED.6
UI_LED8: B1.44, LED.4
UI_LED9: B1.46, LED.2

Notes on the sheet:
Motors
Extensions
Communications
Power
User Interface

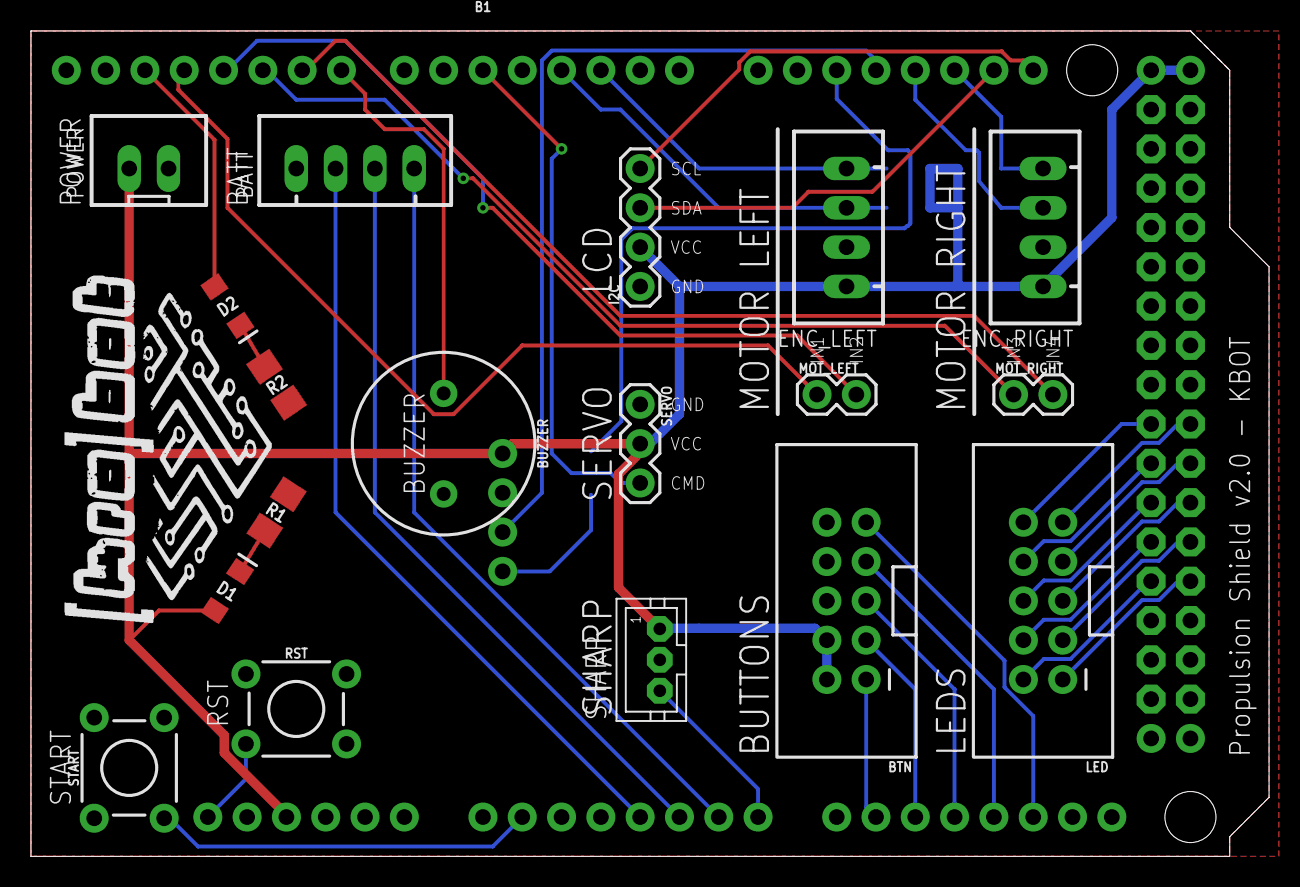
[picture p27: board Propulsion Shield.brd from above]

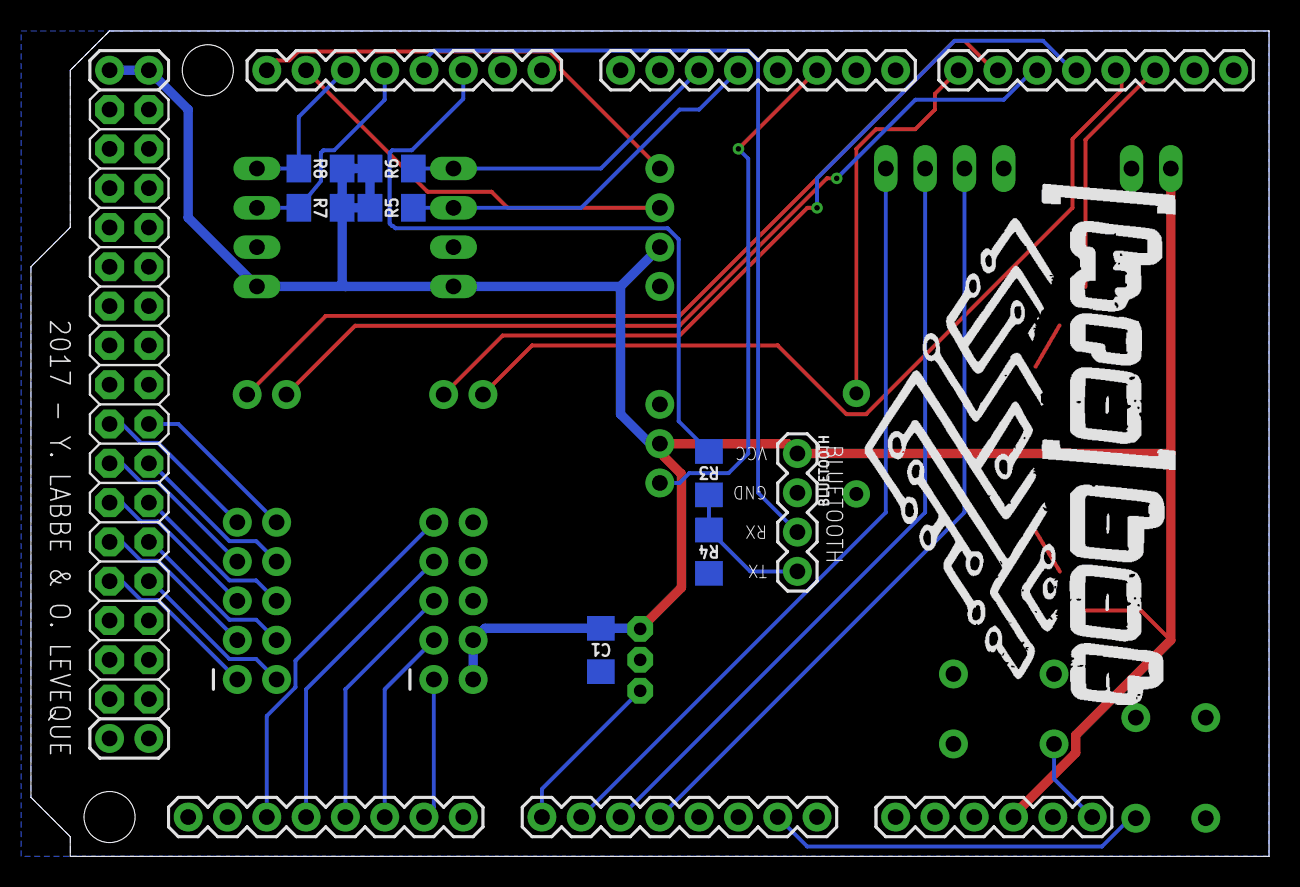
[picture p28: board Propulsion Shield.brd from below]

Board: 2 copper layers, 80.0 x 53.3 mm, 29 parts (9 on the bottom side), 41 nets.

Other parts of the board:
U$1: LOGO_22MM
U$2: LOGO_33MM

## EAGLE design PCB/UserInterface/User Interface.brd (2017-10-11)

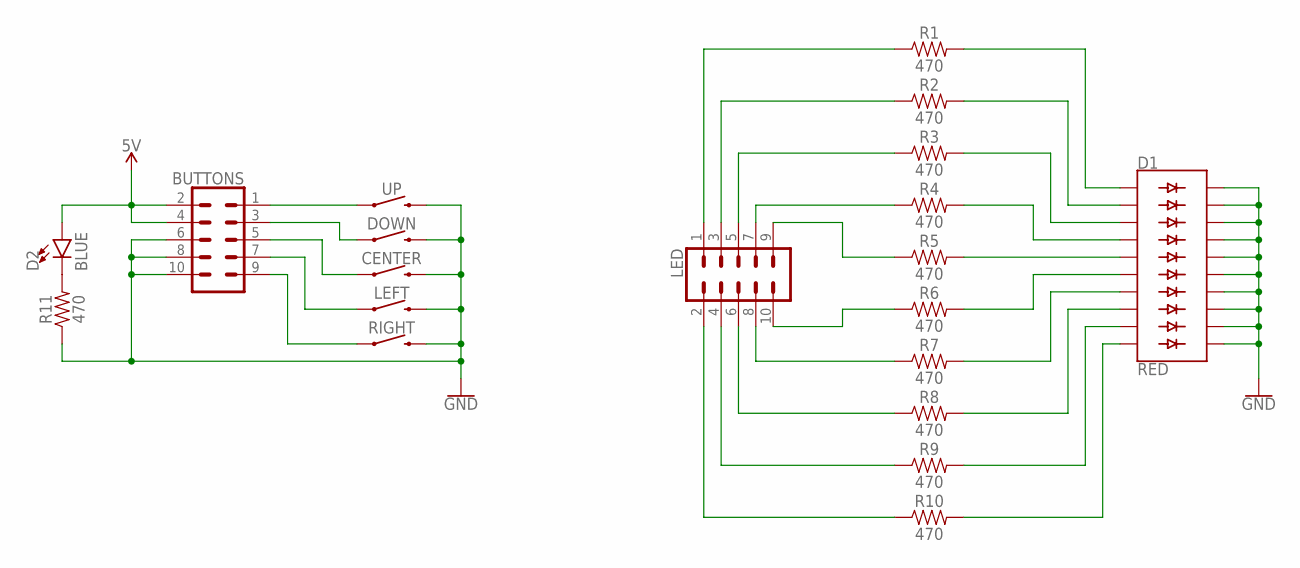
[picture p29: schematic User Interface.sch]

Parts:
BUTTONS: CONN_05X2SHD; 2X5-SHROUDED
CENTER: MOMENTARY-SWITCH-SPST-PTH-6.0MM; TACTILE_SWITCH_PTH_6.0MM
D1: RED; LED_BARGRAPH_10
D2: BLUE; LED-1206
DOWN: MOMENTARY-SWITCH-SPST-PTH-6.0MM; TACTILE_SWITCH_PTH_6.0MM
LED: CONN_05X2SHD; 2X5-SHROUDED
LEFT: MOMENTARY-SWITCH-SPST-PTH-6.0MM; TACTILE_SWITCH_PTH_6.0MM
R1, R2, R3, R4, R5, R6, R7, R8, R9, R10, R11: 470; 1206
RIGHT: MOMENTARY-SWITCH-SPST-PTH-6.0MM; TACTILE_SWITCH_PTH_6.0MM
UP: MOMENTARY-SWITCH-SPST-PTH-6.0MM; TACTILE_SWITCH_PTH_6.0MM

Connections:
5V: BUTTONS.2, BUTTONS.4, D2.A
GND: BUTTONS.6, BUTTONS.8, BUTTONS.10, CENTER.3 (2), D1.11 (C9), D1.12 (C8), D1.13 (C7), D1.14 (C6), D1.15 (C5), D1.16 (C4), D1.17 (C3), D1.18 (C2), D1.19 (C1), D1.20 (C), DOWN.3 (2), LEFT.3 (2), R11.1, RIGHT.3 (2), UP.3 (2)
unnamed: D1.1 (A), R1.2
unnamed: D1.2 (A1), R2.2
unnamed: D1.3 (A2), R3.2
unnamed: D1.4 (A3), R4.2
unnamed: D1.5 (A4), R5.2
unnamed: D1.6 (A5), R6.2
unnamed: D1.7 (A6), R7.2
unnamed: D1.8 (A7), R8.2
unnamed: D1.9 (A8), R9.2
unnamed: D1.10 (A9), R10.2
unnamed: LED.9, R5.1
unnamed: LED.7, R4.1
unnamed: LED.5, R3.1
unnamed: LED.3, R2.1
unnamed: LED.1, R1.1
unnamed: LED.10, R6.1
unnamed: LED.8, R7.1
unnamed: LED.6, R8.1
unnamed: LED.4, R9.1
unnamed: LED.2, R10.1
unnamed: BUTTONS.1, UP.1
unnamed: BUTTONS.3, DOWN.1
unnamed: BUTTONS.5, CENTER.1
unnamed: BUTTONS.7, LEFT.1
unnamed: BUTTONS.9, RIGHT.1
unnamed: D2.C, R11.2

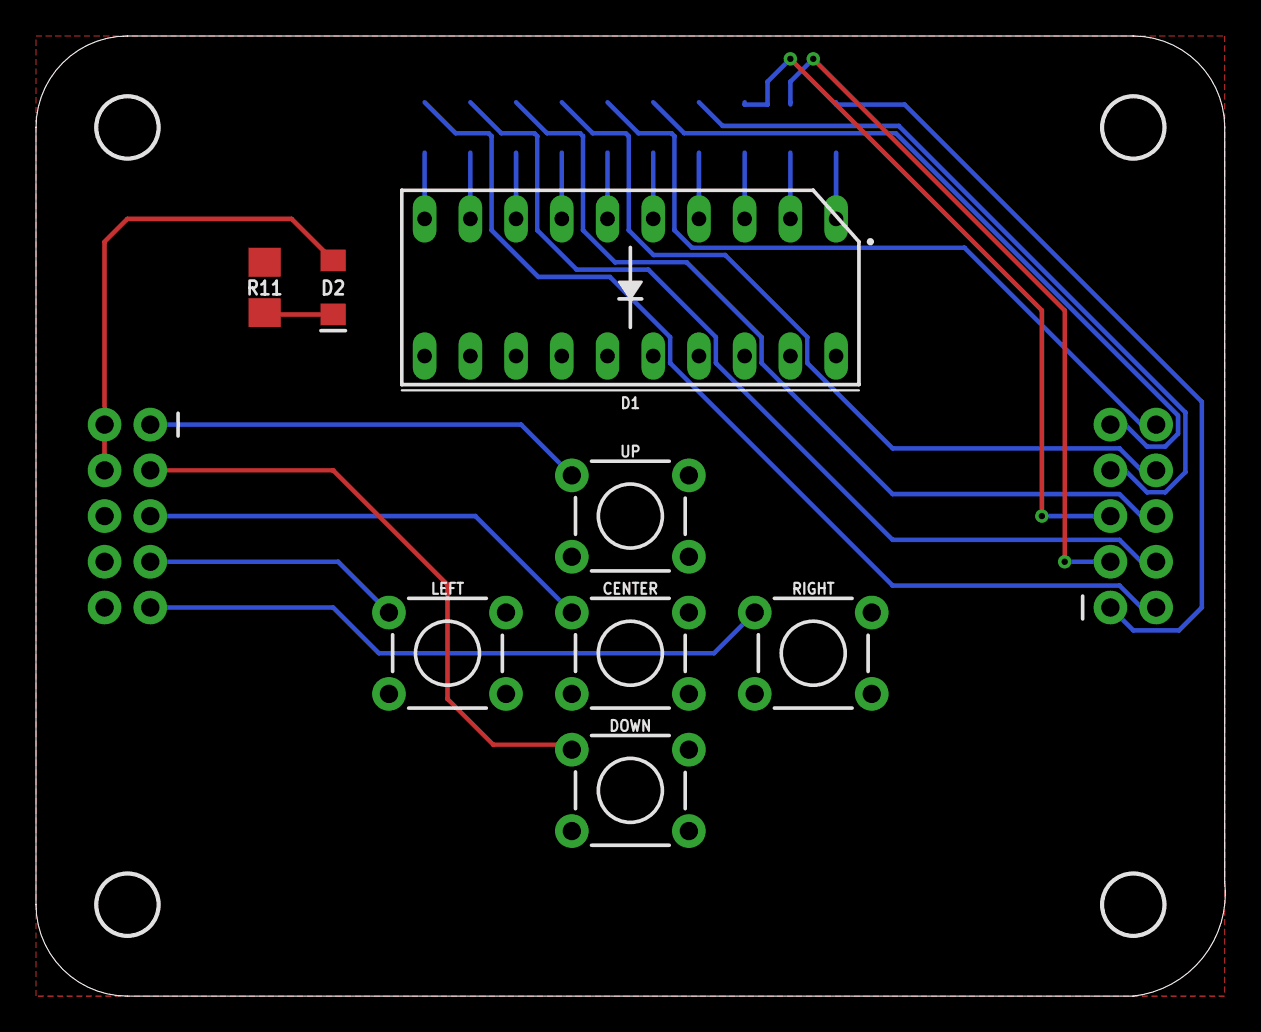
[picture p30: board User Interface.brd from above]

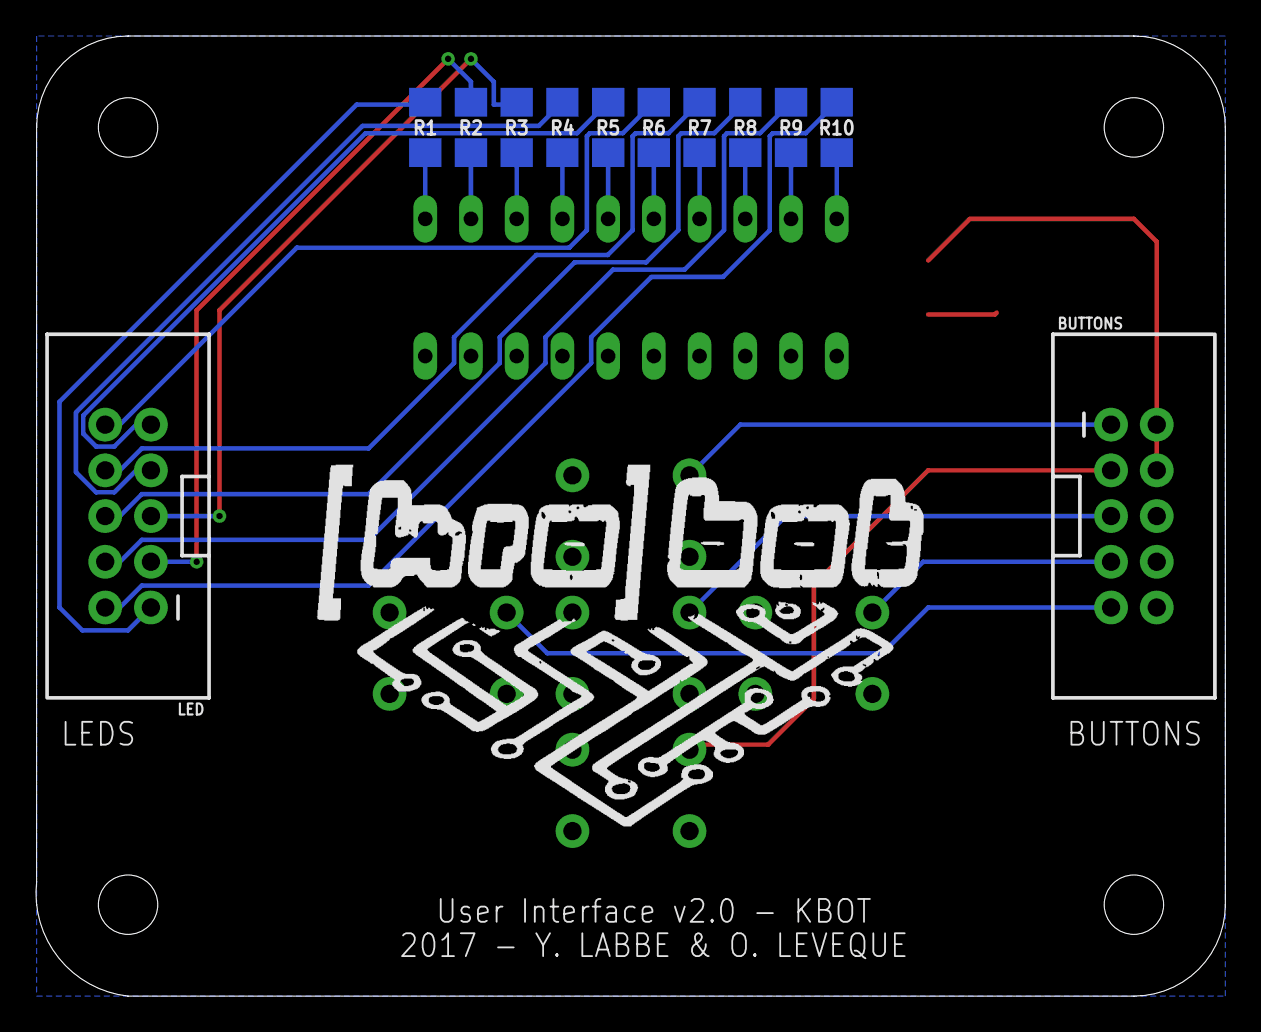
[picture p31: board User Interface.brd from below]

Board: 2 copper layers, 66.1 x 53.3 mm, 25 parts (13 on the bottom side), 28 nets.

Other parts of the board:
U$1, U$2, U$3, U$4: 3,3
U$5: LOGO_33MM

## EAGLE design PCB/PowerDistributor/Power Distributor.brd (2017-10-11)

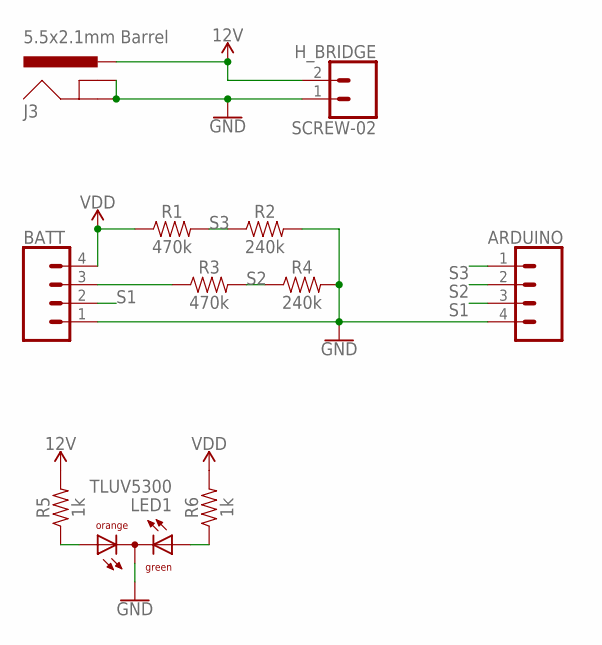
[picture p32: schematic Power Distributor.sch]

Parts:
ARDUINO: JST-XH-04-PIN-LONG-PAD; JST-XH-04-PACKAGE-LONG-PAD
BATT: JST-XH-04-PIN-LONG-PAD; JST-XH-04-PACKAGE-LONG-PAD
H_BRIDGE: SCREW-02
J3: 5.5x2.1mm Barrel; POWER_JACK_SMD
LED1: TLUV5300
R1, R3: 470k; 1206
R2, R4: 240k; 1206
R5, R6: 1k; 1206

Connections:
12V: H_BRIDGE.2, J3.VIN0 (PWR), R5.2
GND: ARDUINO.4, BATT.1, H_BRIDGE.1, J3.GND (GNDBREAK), J3.P$4 (GND), LED1.CC, R2.2, R4.2
unnamed: BATT.3, R3.1
unnamed: LED1.AO, R5.1
unnamed: LED1.AG, R6.1
S1: ARDUINO.3, BATT.2
S2: ARDUINO.2, R3.2, R4.1
S3: ARDUINO.1, R1.2, R2.1
VDD: BATT.4, R1.1, R6.2

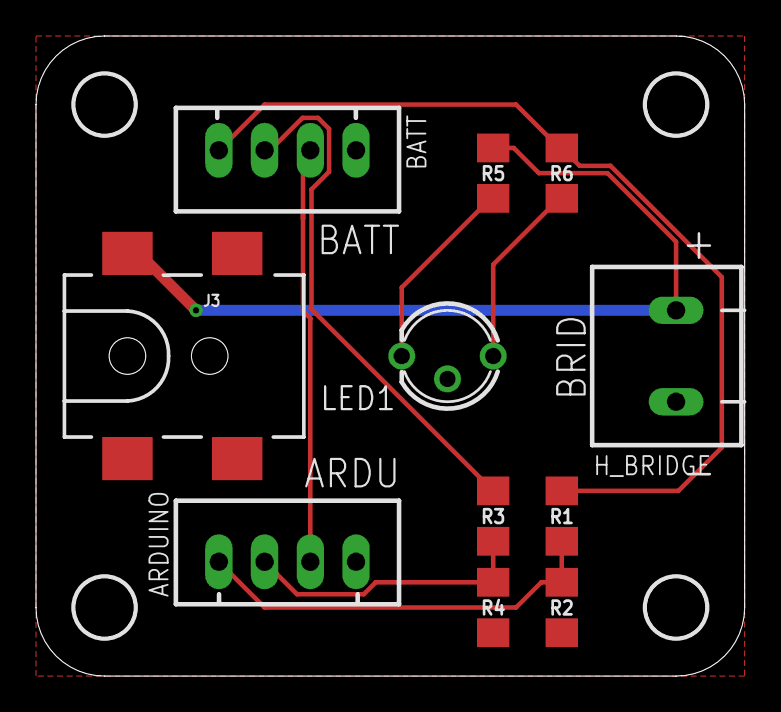
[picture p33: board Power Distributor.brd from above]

Board: 2 copper layers, 39.4 x 35.6 mm, 16 parts (1 on the bottom side), 9 nets.

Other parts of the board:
U$1, U$2, U$3, U$4: 3,3
U$5: LOGO_22MM

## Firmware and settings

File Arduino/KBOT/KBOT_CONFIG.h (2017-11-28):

/************************************************************************
 * File : KBOT.h                                         			    *
 *  Configuration file version 2.0 	  			                        *
 *  Read more : http://github.com/oleveque/KBOT 						*
 *                                                                      *
 * Copyright : (c) 2017, Olivier Lévêque <oleveque@crans.org>      	    *
 ************************************************************************/

#ifndef __KBOT_CONFIG_H
#define __KBOT_CONFIG_H

/* ------------------------- 
  Usefull libraries
------------------------- */

#include <Servo.h>
#include <Wire.h> 
#include <LiquidCrystal_I2C.h> //You need to install this library from http://github.com/marcoschwartz/LiquidCrystal_I2C

/* ------------------------- 
  Config Arduino Méga 2560
------------------------- */

//Motors
#define MOT_LEFT1 	12
#define MOT_LEFT2 	11
#define ENCA_LEFT 	3
#define ENCB_LEFT 	2

#define MOT_RIGHT3 	10
#define MOT_RIGHT4 	9
#define ENCA_RIGHT 	18
#define ENCB_RIGHT 	19

//Serial
#define USB 		Serial
#define BLUETOOTH 	Serial2

//User Interface
#define BUILTIN_LED 13
#define LED0 		47
#define LED1 		45
#define LED2 		43
#define LED3 		41
#define LED4 		39
#define LED5 		38
#define LED6 		40
#define LED7 		42
#define LED8 		44
#define LED9 		46
#define BTN_UP 		A9
#define BTN_DOWN 	A10
#define BTN_CENTER 	A11
#define BTN_LEFT 	A12
#define BTN_RIGHT 	A13
#define BTN_START 	A1

//Battery Monitoring
#define BATT1 		A4
#define BATT2 		A5
#define BATT3 		A6

//Other
#define I2C	 		Wire
#define BUZZER 		8
#define SHARP 		A7
#define SERVO		5

#endif //__KBOT_CONFIG_H

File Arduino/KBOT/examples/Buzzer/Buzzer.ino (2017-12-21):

/************************************************************************
 * File : Buzzer.ino                                                    *
 *  Example : How to play music with a buzzer                           *
 *                                                                      *
 * Copyright : (c) 2017, Olivier Lévêque <oleveque@crans.org>           *
 ************************************************************************/
#include <KBOT_CONFIG.h>

const int c = 261;
const int d = 294;
const int e = 329;
const int f = 349;
const int g = 391;
const int gS = 415;
const int a = 440;
const int aS = 455;
const int b = 466;
const int cH = 523;
const int cSH = 554;
const int dH = 587;
const int dSH = 622;
const int eH = 659;
const int fH = 698;
const int fSH = 740;
const int gH = 784;
const int gSH = 830;
const int aH = 880;
 
void setup() {
  pinMode(BUZZER, OUTPUT);
}
 
void loop() {
  //Play first section
  firstSection();
 
  //Play second section
  secondSection();
 
  //Variant 1
  beep(f, 250);  
  beep(gS, 500);  
  beep(f, 350);  
  beep(a, 125);
  beep(cH, 500);
  beep(a, 375);  
  beep(cH, 125);
  beep(eH, 650);
  delay(500);
 
  //Repeat second section
  secondSection();
 
  //Variant 2
  beep(f, 250);  
  beep(gS, 500);  
  beep(f, 375);  
  beep(cH, 125);
  beep(a, 500);  
  beep(f, 375);  
  beep(cH, 125);
  beep(a, 650);  
  delay(650);
}
 
void beep(int note, int duration) {
  //Play tone on BUZZER
  tone(BUZZER, note, duration);
  delay(duration);
 
  //Stop tone on BUZZER
  noTone(BUZZER);
  delay(50);
}
 
void firstSection() {
  beep(a, 500);
  beep(a, 500);    
  beep(a, 500);
  beep(f, 350);
  beep(cH, 150);  
  beep(a, 500);
  beep(f, 350);
  beep(cH, 150);
  beep(a, 650);
  delay(500);
  beep(eH, 500);
  beep(eH, 500);
  beep(eH, 500);  
  beep(fH, 350);
  beep(cH, 150);
  beep(gS, 500);
  beep(f, 350);
  beep(cH, 150);
  beep(a, 650);
  delay(500);
}
 
void secondSection() {
  beep(aH, 500);
  beep(a, 300);
  beep(a, 150);
  beep(aH, 500);
  beep(gSH, 325);
  beep(gH, 175);
  beep(fSH, 125);
  beep(fH, 125);    
  beep(fSH, 250);
  delay(325);
  beep(aS, 250);
  beep(dSH, 500);
  beep(dH, 325);  
  beep(cSH, 175);  
  beep(cH, 125);  
  beep(b, 125);  
  beep(cH, 250);  
  delay(350);
}

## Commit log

2017-09-19 add pcb files
    [Power Distributor.brd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]
2017-09-28 add cao files
    [1_kbot_v2.DXF, 1_kbot_v2.SLDDRW, 3_kbot_v2.DXF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]
2017-10-10 add PCB pictures
2017-10-11 add screw-02 connector
2017-10-11 update power distributor
    [Power Distributor.brd, Power Distributor.sch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]
2017-10-11 update user interface
    [User Interface.brd, User Interface.sch]
2017-10-11 update propulsion shield
    [Propulsion Shield.brd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]
2017-10-18 Add Arduino examples
2017-10-22 Auto stash before merge of "master" and "origin/master"
    [patin.SLDPRT, patin.STL, support_sharp.STL]
2017-10-22 Update arduino ino
    [support_sharp.STL]
2017-10-22 Rename and reorganize CAO files
    [1-kbot.DXF, 1-kbot.SLDDRW, 3-kbots.DXF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]
2017-11-28 Update BUILTIN_LED pin name
2017-11-29 Add button example
2017-12-11 Add sourcing components
    [Composants.xlsx]
2017-12-11 Reorganize files
    [arduino.SLDPRT, battery.SLDPRT, bridge.SLDPRT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]
2017-12-21 Rename sourcing file
    [Components.xlsx]
2018-01-06 Removed submodule Arduino Libraries/LiquidCrystal_I2C

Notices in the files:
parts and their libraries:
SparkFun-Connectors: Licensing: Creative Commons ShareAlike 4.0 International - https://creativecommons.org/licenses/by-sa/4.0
